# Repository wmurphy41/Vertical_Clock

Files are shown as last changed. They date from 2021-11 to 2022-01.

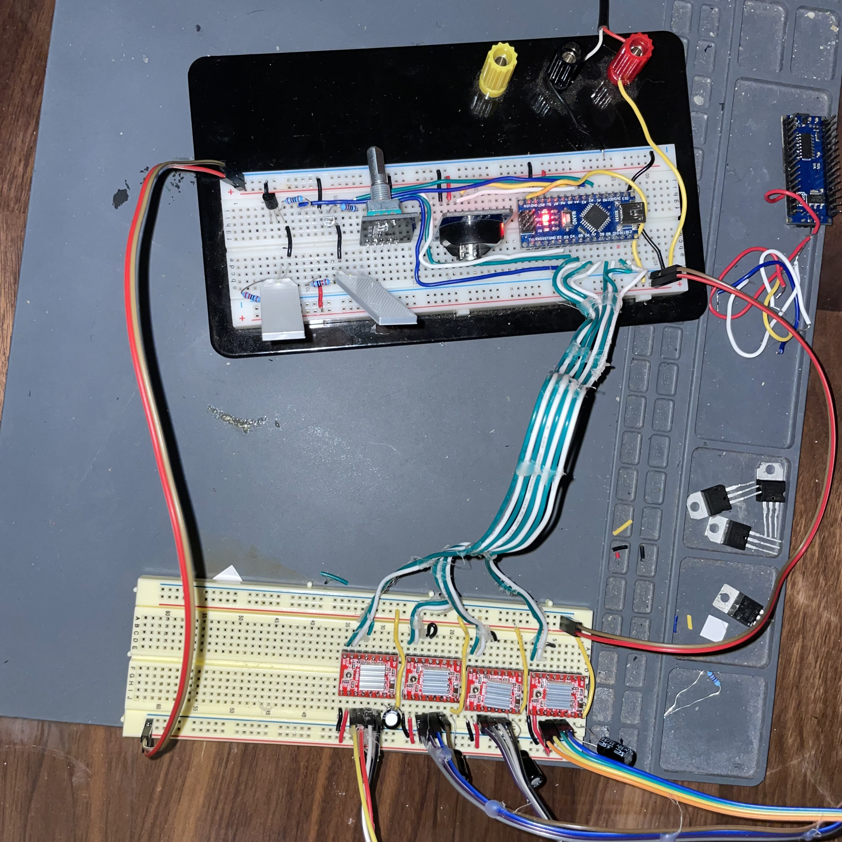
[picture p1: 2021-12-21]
media/Breadboard3.jpg

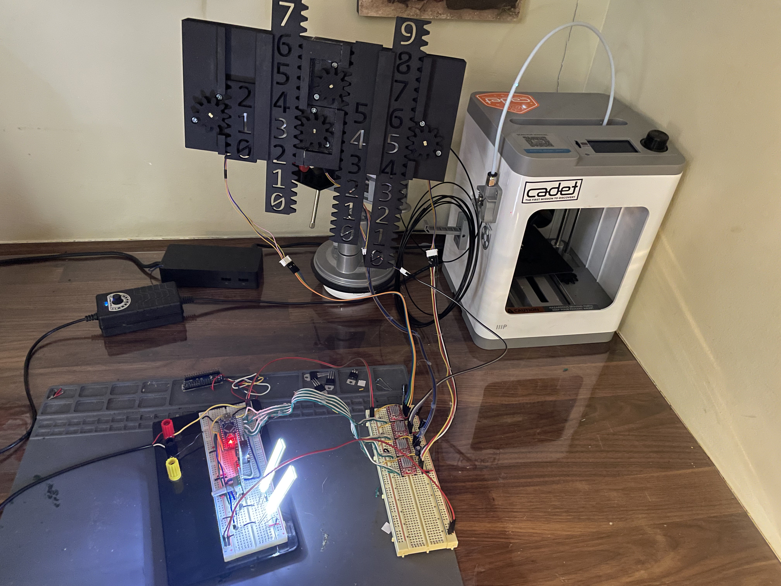
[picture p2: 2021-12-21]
media/Breadboard1.jpg

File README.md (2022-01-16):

# Vertical_Clock
 3D Printed Arduino Vertical Clock

 ## Project Overview
 A clock that tells the time with backlit numbers aligned vertically in four number arrays moved by a rack and pinion mechanism with exposed gears.  The clock mechanism comprises an Arduino microcontroller reading the time from an embedded real-time clock (RTC) and driving the four gears through stepper motors.  A rotary switch allows the user to adjust the time manually.

 #### References and Attributions

 This project is based on this
 [reddit comment](https://www.reddit.com/r/arduino/comments/pnyy3g/i_made_a_physical_version_of_the_oddly_satisfying/) from reddit user [ragusa12](https://www.reddit.com/user/ragusa12).  All props to him for concept and physical design.

 #### Modifications from original
  The original posting did not include wiring diagrams.  I've created them for this project and you can find them in the circuits folder.

 In creating the designs for this project, I've made some changes that I found made the project easier to develop and improved usage:
 - Used A4988 stepper motor driver for the 28BYJ-48 motors instead of their default driver.  It takes a little hacking, but it reduces pin requirement for each motor from 4 to 2.
 - Added a rotary switch for adjusting the time for daylight savings or if the RTC battery dies.  Feature allows you to adjust either minutes or hours.
 - Added a calibration mode.  On first starting, the numbers need to be set to be reset to zero before starting to tell time.  Any time there is a power outage, on restart the system goes to calibration mode with the LEDs blinking.  Once you have set the numbers to zero, you push the rotary switch and it starts telling time.

 #### Background Information
 Reference material I found useful in developing this version:
 - [RTC tutorial](https://howtomechatronics.com/tutorials/arduino/arduino-ds3231-real-time-clock-tutorial/)

## Files
Content of the project folders:
- **code** - Arduino code
- **physical** - STL Files
- **circuits** - electronic circuit design
- **media** - pictures and video of project

## Bill of Materials
- 1x Arduino nano
- 4x [12v 28BYJ-48 stepper motors](https://www.amazon.com/gp/product/B015RQ97W8/ref=ppx_yo_dt_b_asin_title_o00_s00?ie=UTF8&psc=1)
- 2x [small led backlight module](amazon.com/gp/product/B01N6XME2Q/ref=ox_sc_act_title_1?smid=ATVPDKIKX0DER&psc=1)
- 4x [A4988 stepper motor drivers](https://www.amazon.com/gp/product/B09FQ3G5XQ/ref=ppx_yo_dt_b_asin_title_o00_s00?ie=UTF8&psc=1)
- 1x [RTC module](https://www.amazon.com/gp/product/B07XY2STMF/ref=ox_sc_act_title_2?smid=A2JLTKYCWT3GQ2&psc=1)
- 1x [12v power supply](https://www.amazon.com/gp/product/B01GD4ZQRS/ref=ppx_yo_dt_b_asin_title_o00_s00?ie=UTF8&th=1)
- 1x [rotary switch](https://www.amazon.com/dp/B07M631J1Q/ref=cm_sw_em_r_mt_dp_0N9X54H6T59A8A89X890?_encoding=UTF8&psc=1)
- 4x 100 mF capacitors
- 2x npn transistors
- 4x 1k ohm resistors
- PLA cable for 3D printer
- 1x C2032 battery for the RTC
- hot glue gun and glue
- nylon spacers and nuts

## Installation
Instructions for building the printed components, electronics, software, and assembly of the Vertical Clock.

#### Printed Components
Print all components in PLA.

| Component  | Count | Color |
| --- | ----: | ----- |
| BaseA (1)  | 1 | black |
| BaseB (1)  | 1 | black |
| Gear (4) | 4 | black |
| LightBrick | 4 | white |
| FullDigit  | 2 | black |
| 6Digit | 1 | black |
| 3Digit | 1 | black |
| knob | 1 | black |

#### Electronics
1. Hack the stepper motors.  The 28BYJ-48 stepper motors are unipolar and the
A4988 driver only works with bipolar motors.  Take the red wire out of the connector,
cut it near the motor and discard.  Reorder the wires in the connector so that
are in order orange, yellow, pink, blue, reading left to right when looking at
the flat side of the connector.  More info on this step [here](https://www.instructables.com/28BYJ-48-5V-Stepper-Motor-and-A4988-Driver/)  I ignored adjusting
the current potentiometer.
2. Build prototype board based on circuit diagrams.  Pins.h matches the pin
configuration of the prototype circuit diagram.  Breadboard diagram used different pins.

#### Code
1. Vertical_Clock - Main folder for final product.  Move this folder to Arduino environment, compile, and upload.  You'll need to install into your Arduino environment all of the libraries referenced in the include files.
  - vertical_clock.ino - primary Arduino file
  - ClockDigit.h and ClockDigit.cpp - class files for controlling stepper motors
  - ClockState.h and ClockState.cpp - class files for managing system state of clock.
2. led_via_npn - folder containing code for breadboarding the led
3. rotary_and_rtc - folder containing code for testing rtc and rotary switch modules
4. stepper - folder containing code for testing stepper motors and clock digits

## Assembly
1. Attach the two halves of the case with Gorilla glue.  Have acetone or rubbing
alcohol on hand to clean up the overspills
2. Install white backplates and affix with hot glue
2. Install motors with bolts and nuts and press on gears
3. Affix LEDs with hot glue
4. Drill hole in case and attach Rotary Switch with nut.  Affix knob.
5.  Affix power socket with hot glue
6. Affix circuit boards with nylon hex spacers hot glued to case and secure with
nylon nuts.

## Usage
Operating instructions

#### Setup and calibration
- Plug in power
- Both lights will flash slowly.  It is in calibration modes
- Gently raise or lower the number bars until each number is set to zero
- Depress the rotary switch to move into normal mode.  
- Both lights will turn on and stop blinking
- The number bars will start moving until the numbers match the current time
in the RTC.

Note that if the clock loses power while running, when power is restored, it will
start in calibration mode.  Use the steps above to set the numbers to zero
before pressing the switch to move it into normal mode.

#### Adjusting time
- _Setting the Minutes:_ Depress the rotary switch.  The clock is now in adjust
minutes mode.  The hour light will turn off
and the minutes light will blink quickly.  Slowly turn the rotary switch.  Each
click will adjust one minute.  Clockwise will add minutes. Counterclockwise will
subtract.  There will be a slight delay from turning the dial to when the numbers
move.  Once the numbers start moving, they will continue until stopped.  If
you turn the dial while the numbers are moving, the numbers will finish the move
until then moving to the new number.  You can only adjust the minutes up to 59
or down to 0.  Once at 59, continuing to turn clockwise will have no effect.  
Once at 0, continuing to turn counterclockwise will have no effect.
- _Setting the Hour:_  From adjust minutes mode, depress the rotary switch.
The clock is now in adjust hour mode.  The minute light will turn off and the
hour light will blink quickly.  Adjust the hours just as with the minutes.  As
with the minutes, you can only adjust the hours up to 23 and down to 0. They
won't roll over from 0 to 23 or from 23 to 0.
- _Returning to Normal Mode:_ From adjust hour mode, depress the switch once.
Both lights will turn on.

## Ideas for Future Enhancements
1. Shift from 24 to 12 hour module.  May need an LED to indicate AM/PM
2. Enable a temperature mode.  Just read the temp from the RTC module and display with the digits. Would need to change the design of the number bars.

## Contributing
- Pull requests are welcome. For major changes, please open an issue first to discuss what you would like to change.
- Please make sure to test updates as appropriate.

## License
[MIT](https://choosealicense.com/licenses/mit/)

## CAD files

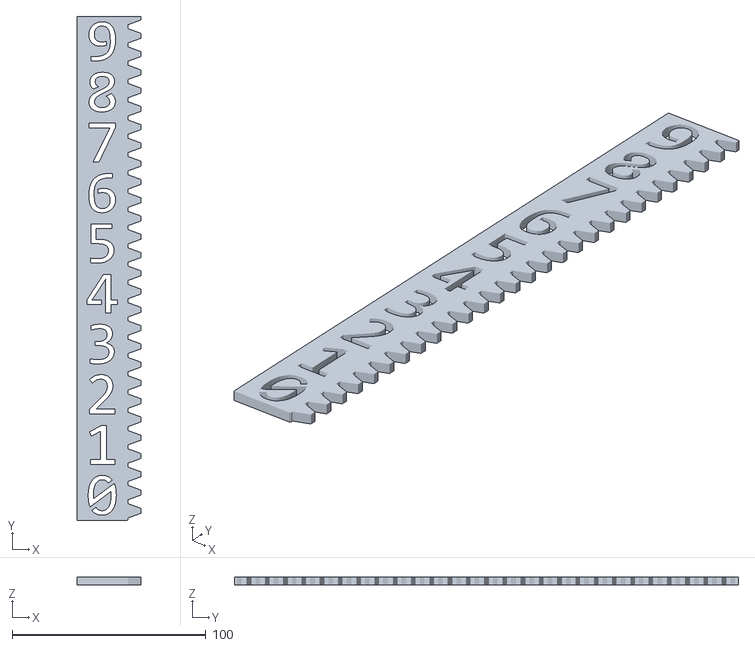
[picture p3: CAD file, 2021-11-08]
physical/FullDigit.stl
33.0 x 260.0 x 4.00

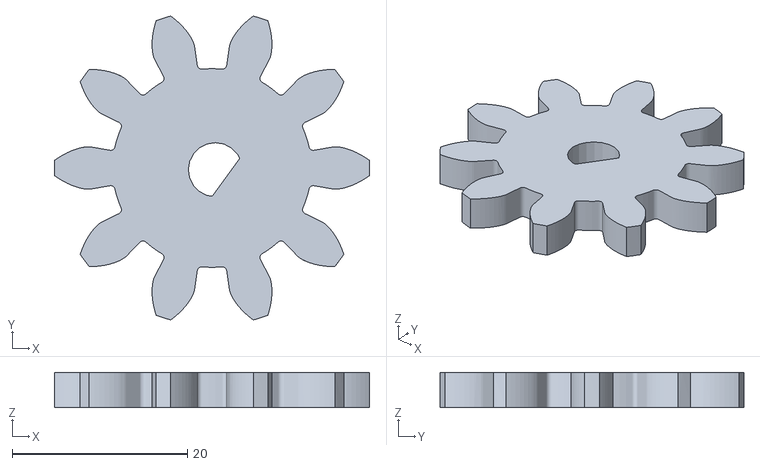
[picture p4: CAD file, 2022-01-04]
physical/Knob.stl
36.0 x 34.7 x 4.00

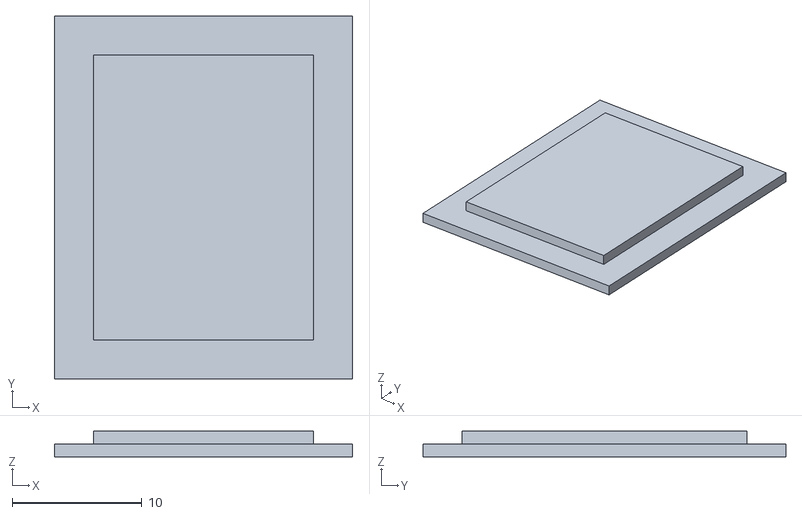
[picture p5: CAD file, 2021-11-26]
physical/LightBrick2.stl
23.0 x 28.0 x 2.00

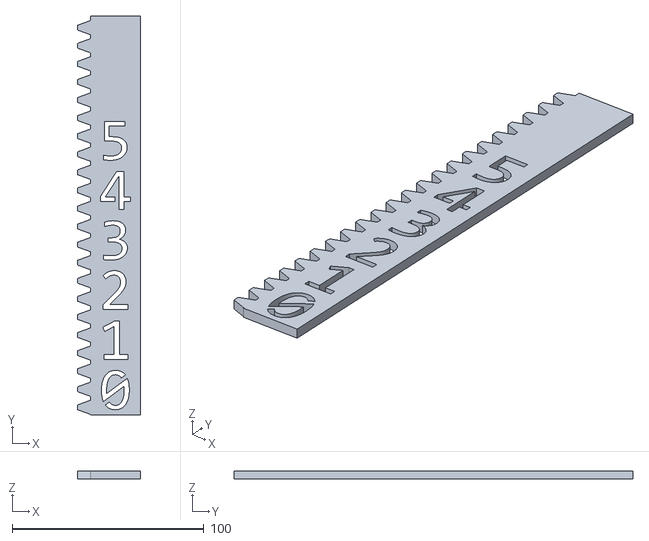
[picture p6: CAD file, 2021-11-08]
physical/6Digit.stl
32.7 x 208.0 x 4.00

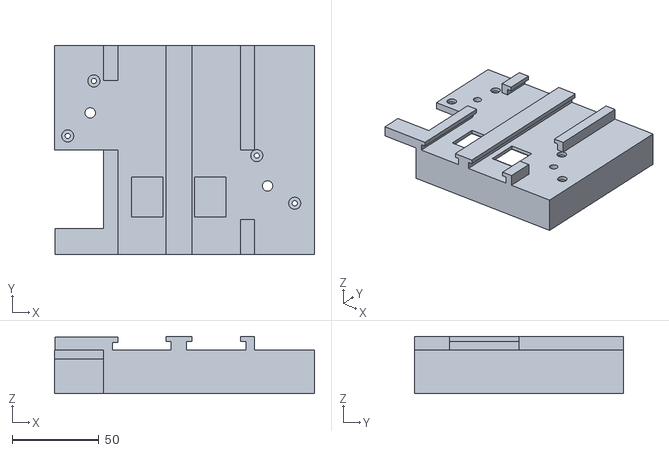
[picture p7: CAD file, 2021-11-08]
physical/BaseA.stl
149.5 x 120.0 x 33.0

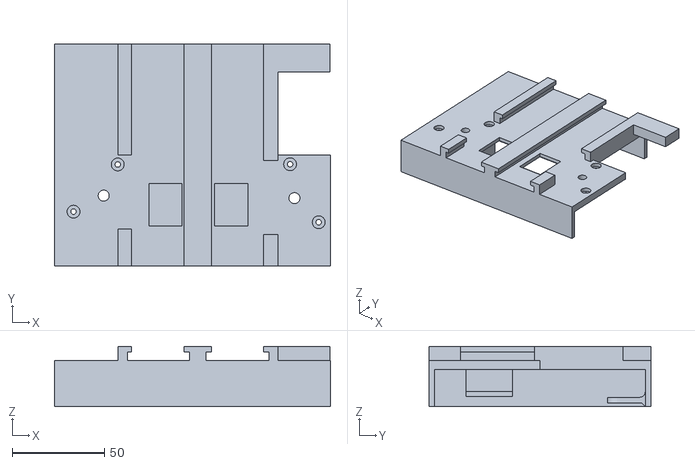
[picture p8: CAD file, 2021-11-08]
physical/BaseB.stl
149.4 x 120.0 x 32.5

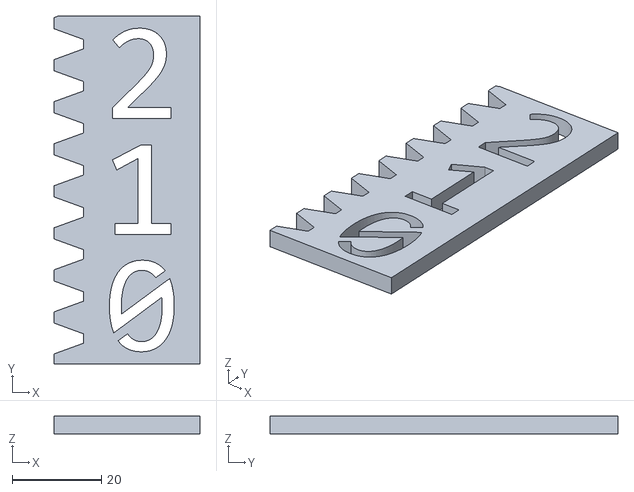
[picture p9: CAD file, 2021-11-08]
physical/3Digit.stl
32.6 x 78.0 x 4.00

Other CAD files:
physical/LightBrick.stl
physical/Gear.stl

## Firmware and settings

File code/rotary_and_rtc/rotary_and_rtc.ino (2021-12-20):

// Date and time functions using a DS1307 RTC connected via I2C and Wire lib

#include <DS3231.h>
#include <Wire.h>

//Define the pin connection
const int CLK_PIN = 2 ;        //CLK->D2.  We will monitor for interrupt
const int SW_PIN = 3 ;         //SW->D3.  We will monitor for interrupt
const int DT_PIN  = 4 ;        //DT->D4 
const int MINUTE_LED = A1 ;
const int HOUR_LED = A2 ;


// Globals
// State engine

enum { normal = 0, edit_minutes = 1, edit_hours = 2, dark_mode = 3 } sketchState ;

// Rotary Switch
volatile int lastCLK = 0;                      
volatile int rotaryCount = 0 ;
volatile bool switchClicked = false ; 

DS3231 realTimeClock;                 // Real time clock

void setup () {
    Serial.begin(57600);
    Serial.println("Starting setup...") ;
  
    // Setup RTC
    Wire.begin();

    // Set up LEDs
    pinMode(MINUTE_LED, OUTPUT);
    pinMode(HOUR_LED, OUTPUT);
    
    // Setup Rotary Switch
    pinMode(SW_PIN, INPUT);
    digitalWrite(SW_PIN, HIGH);
    pinMode(CLK_PIN, INPUT);
    pinMode(DT_PIN, INPUT);
    attachInterrupt(digitalPinToInterrupt(CLK_PIN), DialRotated_ISR, CHANGE);
    attachInterrupt(digitalPinToInterrupt(SW_PIN), SwitchClicked_ISR, FALLING);

    // Set initial state
    sketchState = normal ; 
    digitalWrite (MINUTE_LED, HIGH);
    digitalWrite (HOUR_LED, HIGH);
  
    Serial.println("...completed setup.") ;
}

void loop () {

    // Check if switch was clicked
    if (switchClicked) {
      switchClicked = false ;
      sketchState = (sketchState + 1) % 4 ;
        
      Serial.println("Switch clicked...") ; 
      Serial.print("New sketchState is... ") ;
      Serial.println(sketchState) ;
       
      switch (sketchState) {
        case normal :
          digitalWrite (MINUTE_LED, HIGH);
          digitalWrite (HOUR_LED, HIGH);
          break ;
        case edit_minutes :
          digitalWrite (MINUTE_LED, HIGH);
          digitalWrite (HOUR_LED, LOW);
          break ;
        case edit_hours :
          digitalWrite (MINUTE_LED, LOW);
          digitalWrite (HOUR_LED, HIGH);
          break ;
         case dark_mode :
          digitalWrite (MINUTE_LED, LOW);
          digitalWrite (HOUR_LED, LOW);
          break ;             
      }
    }
    
    
    // Every 3 seconds
    // - Check clock
    // - Check if switch was rotated to adjust time
    static long int lastTimeRan = 0 ;
    if ((millis() - lastTimeRan) > 3000) {
      lastTimeRan = millis() ;

      // Printing Time
      bool hour12, pmTime ;
      Serial.print(realTimeClock.getHour(hour12, pmTime), DEC);
      Serial.print(':');
      Serial.print(realTimeClock.getMinute(), DEC);
      Serial.print(':');
      Serial.print(realTimeClock.getSecond(), DEC);
      Serial.println();
  
      // If the switch has been rotated since the last check-in
      // Adjust minutes
      if (rotaryCount |= 0) {
        int newMinutes = realTimeClock.getMinute() + rotaryCount ;
        newMinutes = max ( min(newMinutes, 59), 0) ;
        
        Serial.print("Adding " ) ;
        Serial.print(rotaryCount) ;
        Serial.print(" minutes to set new minutes to ") ;
        Serial.println(newMinutes) ;
        
        realTimeClock.setMinute(newMinutes) ;  
        realTimeClock.setSecond(0) ;            // Always set seconds to zero when adjusting minutes
        rotaryCount = 0 ;
      }
    }
}

//The interrupt handlers
void DialRotated_ISR()
{
  int clkValue = digitalRead(CLK_PIN) ;       //Read the CLK pin level
  int dtValue = digitalRead(DT_PIN) ;         //Read the DT pin level
  if (lastCLK != clkValue)    {
    lastCLK = clkValue;
    if (lastCLK % 2)                        // Increment count every 2 clicks
      rotaryCount += (clkValue != dtValue ? 1 : -1) ;  //CLK and inconsistent DT + 1, otherwise - 1
  }
}

void SwitchClicked_ISR()
{
  static long timeLastClick = 0 ;

  if ( millis() - timeLastClick > 500 ) {
    switchClicked = true ;
    timeLastClick = millis() ;
  }
} 

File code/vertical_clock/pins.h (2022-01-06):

#ifndef PINS_H
#define PINS_H

//Define the pin connections for the Rotary Switch
const int SW_PIN =      2 ;        //monitor for interrupt
const int CLK_PIN =     3 ;        //monitor for interrupt
const int DT_PIN  =     4 ;

//Define the pin connections for the Stepper Drivers
const int DIRPIN_MINUTE_ONES = 5 ;
const int STEPPIN_MINUTE_ONES = 6 ;
const int DIRPIN_MINUTE_TENS = 7 ;
const int STEPPIN_MINUTE_TENS = 8 ;
const int DIRPIN_HOUR_ONES = 9 ;
const int STEPPIN_HOUR_ONES = 10 ;
const int DIRPIN_HOUR_TENS = 11 ;
const int STEPPIN_HOUR_TENS = 12 ;
const int ENABLE_PIN =  13 ;       // Shared enable pin for all steppers

//Define the pin connections for the real time clock
const int SDA_PIN =     A4 ;       // Used by the RTC (preset config)
const int SCL_PIN =     A5 ;       // Used by RTC (preset config)

// Pins for LEDs
const int MINUTE_LED =  A1 ;
const int HOUR_LED =    A2 ;


#endif //PINS_H

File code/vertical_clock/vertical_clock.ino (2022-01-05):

/*
 *  Vertical Clock
 *
 *  Use real time clock to keep track of time.
 *  Drives four stepper motors to move clock digits to match time.
 *  Collects user input from a rotary switch to change modes and adjust
 *  time.
 */

#include <DS3231.h>
#include <Wire.h>
#include "ClockState.h"
#include "ClockDigit.h"
#include "pins.h"         // pin assignments


// Logic constants
const int LOOP_TIMER = 3000 ;     // Time between checks for digit change (3s)

// Globals
// Clock digit and stepper motor
// Local definitions of the static class members
int ClockDigit::enable_pin { ENABLE_PIN } ;
int ClockDigit::sp = 0 ;
ClockDigit *ClockDigit::digit_stack[NUM_DIGITS] ;
// clock digit objects
ClockDigit minute_ones (ClockDigit::REV, STEPPIN_MINUTE_ONES, DIRPIN_MINUTE_ONES) ;
ClockDigit minute_tens (ClockDigit::FWD, STEPPIN_MINUTE_TENS, DIRPIN_MINUTE_TENS) ;
ClockDigit hour_ones (ClockDigit::REV, STEPPIN_HOUR_ONES, DIRPIN_HOUR_ONES) ;
ClockDigit hour_tens (ClockDigit::FWD, STEPPIN_HOUR_TENS, DIRPIN_HOUR_TENS) ;

// State engine
ClockState clockState(HOUR_LED, MINUTE_LED) ;

// Rotary Switch
volatile int lastCLK = 0;
volatile int rotaryCount = 0 ;
volatile bool switchClicked = false ;

// RTC
DS3231 realTimeClock;


/* Setup()
 *
 *
 */
void setup () {
    Serial.begin(57600);
    Serial.println("Starting setup...") ;

    // Setup RTC
    Wire.begin();

    // Set up LEDs and enable pin for the steppers
    ClockDigit::setup() ;
    clockState.setup() ;

    // Setup Rotary Switch
    pinMode(SW_PIN, INPUT);
    digitalWrite(SW_PIN, HIGH);
    pinMode(CLK_PIN, INPUT);
    pinMode(DT_PIN, INPUT);
    attachInterrupt(digitalPinToInterrupt(CLK_PIN), DialRotated_ISR, CHANGE);
    attachInterrupt(digitalPinToInterrupt(SW_PIN), SwitchClicked_ISR, FALLING);

    Serial.println("...completed setup.") ;
}

/*
 * loop()
 * - If the switch was clicked, increment the clock state
 * - If we're in calibrate mode, then jump out of loop (no actions)
 * - Every LOOP_TIMER milliseconds,
 *    - Check if switch was rotated to adjust time
 *    - Update dials to match clock time
 * - Move stepper motors one step until all match
 *     the digits where they are supposed to be.
 */
void loop () {

    static bool firstrun = true ;

    // Check if switch was clicked
    if (switchClicked) {
      switchClicked = false ;
      clockState.incrementState() ;
    }
    clockState.setLEDs() ;

    // If we're still in calibrate state - just end loop now.
    if   (clockState.getState() == ClockState::calibrate_mode) {
      if (firstrun) {
        Serial.println("calibrate mode") ;
        PrintTime() ;
        firstrun = false ;
      }
      return ;
    }

    // Every LOOP_TIMER milliseconds
    // - Check if switch was rotated to adjust time
    // - Update dials to match clock time
    static long int lastTimeRan = 0 ;
    if ((millis() - lastTimeRan) > LOOP_TIMER) {
      lastTimeRan = millis() ;

      // if switch rotated adjust time
      if (rotaryCount != 0)      {

        switch (clockState.getState()) {
          case ClockState::edit_minute :  {
              int newMinute = realTimeClock.getMinute() - rotaryCount ;
              newMinute = max ( min(newMinute, 59), 0) ;
              realTimeClock.setMinute(newMinute) ;
              realTimeClock.setSecond(0) ;            // Always set seconds to zero when adjusting minutes
              rotaryCount = 0 ;
            }
            break ;

          case ClockState::edit_hour : {
              bool hour12, pmTime ;
              int newHour = realTimeClock.getHour(hour12, pmTime) - rotaryCount ;
              newHour = max ( min(newHour, 24), 0) ;
              realTimeClock.setHour(newHour) ;
              rotaryCount = 0 ;
            }
            break ;

          default:
            rotaryCount = 0 ;   // normal and dark mode, ignore clicks
        }
      }

      // Adjust dials to match time
      bool hour12, pmTime ;
      int this_hr = realTimeClock.getHour(hour12, pmTime) ;
      int this_min = realTimeClock.getMinute() ;

      minute_ones.setToDigit(this_min % 10);
      minute_tens.setToDigit(this_min / 10);
      hour_ones.setToDigit(this_hr % 10);
      hour_tens.setToDigit(this_hr / 10);
      PrintTime() ;
   } // end set dials to current time

  // Move stepper motors one step until all match
  // the digits where they are supposed to be.
  ClockDigit::run_all() ;

}

/* Interupt handlers
 *
 *  DialRotated_IRS - updates globals to track number of clicks rotary is turned
 *  SwitchClicked_IRS - Sets global flag when the switch was clicked
 */
//The interrupt handlers
void DialRotated_ISR()
{
  int clkValue = digitalRead(CLK_PIN) ;       //Read the CLK pin level
  int dtValue = digitalRead(DT_PIN) ;         //Read the DT pin level
  if (lastCLK != clkValue)    {
    lastCLK = clkValue;
    if (lastCLK % 2)                        // Increment count every 2 clicks
      rotaryCount += (clkValue != dtValue ? 1 : -1) ;  //CLK and inconsistent DT + 1, otherwise - 1
  }
}

void SwitchClicked_ISR()
{
  static long timeLastClick = 0 ;

  if ( millis() - timeLastClick > 500 ) {  // Avoids spurious double reads of same clicks
    switchClicked = true ;
    timeLastClick = millis() ;
  }
}


 /*
  *  helper functions.  For debugging only.
  */
 void PrintTime() {
    bool hour12, pmTime ;

    Serial.print("time: ");
    Serial.print(realTimeClock.getHour(hour12, pmTime), DEC);
    Serial.print(':');
    Serial.print(realTimeClock.getMinute(), DEC);
    Serial.print(':');
    Serial.print(realTimeClock.getSecond(), DEC);
    Serial.println();
 }

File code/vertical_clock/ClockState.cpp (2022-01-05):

/*
 *  ClockState methods:
 *  - constructor - stores LED pins
 *  - setup - initializes LEDs and enable PIN
 *  - IncrementState - moves to next state when switch is triggered and updates lights
 *  - GetState - returns current state of the sketch
 */
 #include "ClockState.h"
 #include <arduino.h>

 ClockState::ClockState(int h, int m) {
  hourLED = h ;
  minLED = m ;
  sketchState = calibrate_mode ;
 }

void ClockState::setup() {
    pinMode(minLED, OUTPUT);
    pinMode(hourLED, OUTPUT);
    digitalWrite (minLED, LOW);
    digitalWrite (hourLED, LOW);
 }


// Cycles through the clock states
// calibrate -> normal -> edit_hour -> edit_minute
//                ^                        |
//                +------------------------+
void ClockState::incrementState() {

   if (sketchState == calibrate_mode) {
     sketchState = normal ;
   }
   else {
      sketchState = (sketchState + 1) % 3 ;
   }
}

// Set the LEDs to match the state
//  - Normal - both on
//  - Edit Minutes - hour off, minute fast blinking
//  - Edit Hours - minute off, hour fast blinking
//  - Calibration mode - both slow blinking
void ClockState::setLEDs() {

    switch (sketchState) {
    case normal :
      digitalWrite (minLED, HIGH);
      digitalWrite (hourLED, HIGH);
      break ;
    case edit_minute :
      if (millis() % (2*FAST_BLINK) > FAST_BLINK ) {
        digitalWrite (minLED, LOW);
      }
      else {
        digitalWrite (minLED, HIGH);
      }
      digitalWrite (hourLED, LOW);
      break ;
    case edit_hour :
      digitalWrite (minLED, LOW);
      if (millis() % (2*FAST_BLINK) > FAST_BLINK ) {
        digitalWrite (hourLED, LOW);
      }
      else {
        digitalWrite (hourLED, HIGH);
      }
      break ;
    case calibrate_mode :
      if (millis() % (2*SLOW_BLINK) > SLOW_BLINK ) {
        digitalWrite (minLED, LOW);
        digitalWrite (hourLED, LOW);
      }
      else {
        digitalWrite (minLED, HIGH);
        digitalWrite (hourLED, HIGH);
      }
      break ;
   }
}

int ClockState::getState() {
  return sketchState ;
}

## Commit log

2021-11-08 3D Printed / Arduino-driven digital clock
    An Arduino nano controls stepper motors to drive rack and pinion gears to raise and lower bars so that the current time is aligned in front of an LED light bar.
    [3Digit.stl, 6Digit.stl, BaseA.stl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]
2021-11-08 3D-printed Arduino-driven digital clock
    Aduino controls stepper motors that drive 3-D printed rack and pinion gears to display the time.
2021-11-26 Updated readme.md. Moved printlist into readme.
    [LightBrick2.stl]
2021-11-27 Added first breadboard diagram
    [vertical_clock.fzz]
2021-12-05 Breadboard version 1
    Components enabled
    - LEDs
    - Rotary Switch
    - RTC
    Logic:
    - State is managed through rotary switch
    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
2021-12-21 Added calibrate mode
    On first starting, the numbers need to be set to be reset to zero before starting to tell time. Any time there is a power outage, on restart the system goes to calibration mode with the LEDs blinking. Once you have set the numbers to zero, you push the rotary switch and it starts telling time.
    [vertical_clock.fzz]
2022-01-04 Fully functional prototype
    Fully functioning prototype code. Added circuit diagram for prototype board.
    [Knob.stl, vertical_clock.fzz, vertical_clock_breadboard.fzz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]
2022-01-06 Added resistor to LED circuit
    Added 1k resistor between Arduino and control pin of each transistor.
    [vertical_clock_breadboard.fzz, vertical_clock_prototype_board.fzz]
